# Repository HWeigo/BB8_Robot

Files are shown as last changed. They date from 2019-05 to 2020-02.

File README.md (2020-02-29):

# BB-8 Robot  
##### Keep Calm and May the Force Be With You  

## Overview  
This repository contains both codes and CAD model for the BB-8 robot. The main goal of this project is to redesign BB-8 robot’s inner mechanism, as well as the control algorithm, to improve its balance. A two-wheel self-balancing robot was built and tested first. After then, we reassemble it to the final BB-8 robot by changing the chassis and adding other components. STM32F407 was used as the microcontroller in this project, while CubeMX was utilized for STM32’s configuration and FreeRTOS was implemented as the kennel. /Model includes all the parts for both self-balancing car and our final BB-8 robot (based on SolidWorks 2018). Other electron components and stuffs are listed in /reference.  

## CAD and Physical Prototype

#### Two-wheel Self-balancing Robot
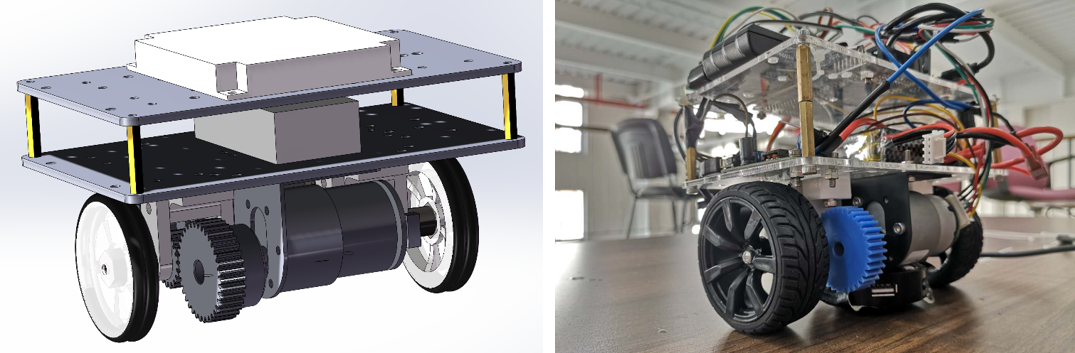
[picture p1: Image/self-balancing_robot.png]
Two-wheel Self-balancing Robot
  
#### BB-8 Robot
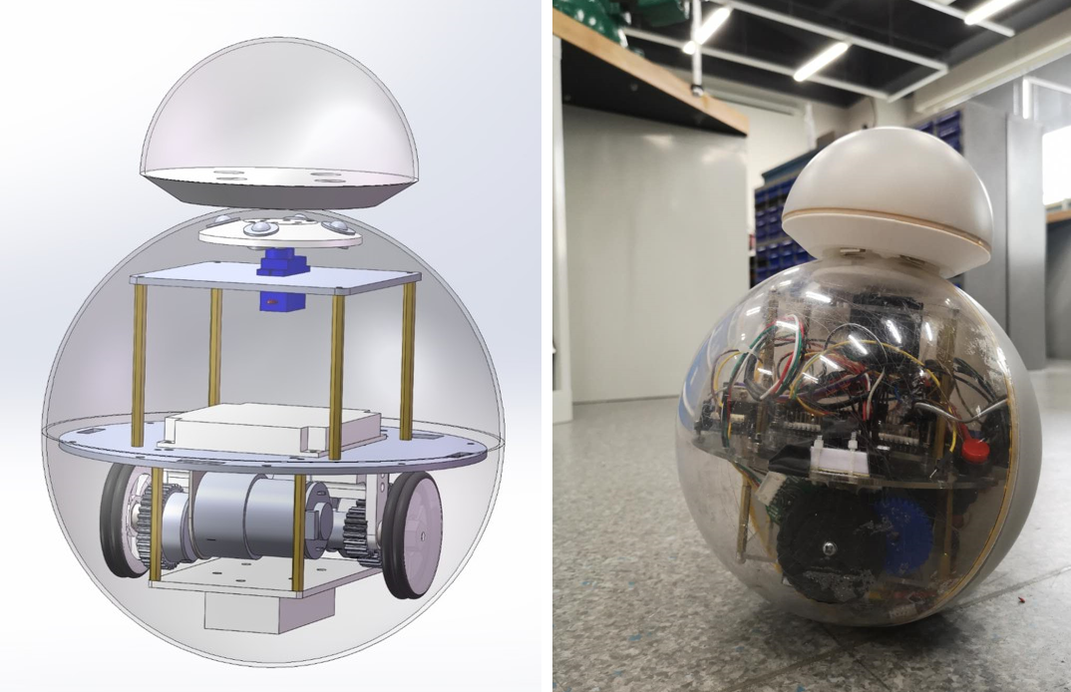
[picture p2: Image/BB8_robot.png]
BB-8 Robot
  

## Electronics Schematic  
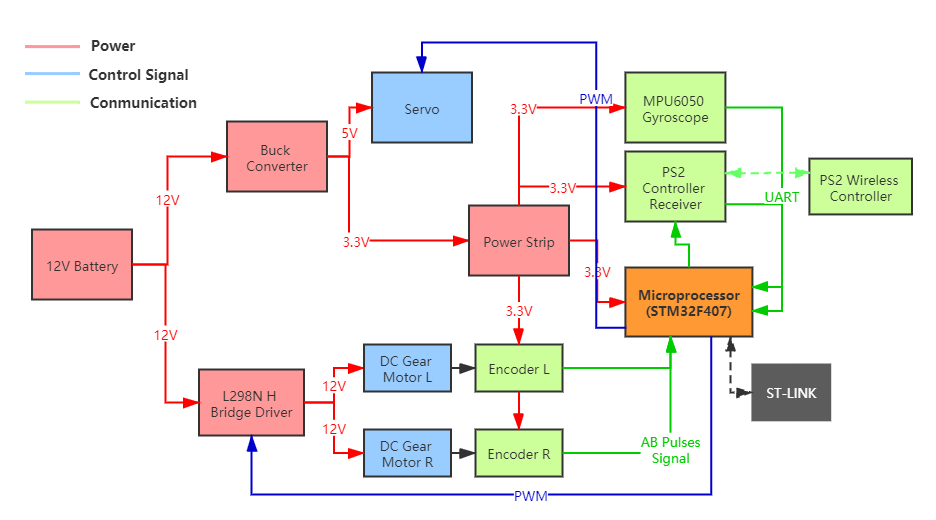
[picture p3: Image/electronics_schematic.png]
Electronics Schematic
  

## FreeRTOS Task Diagram  
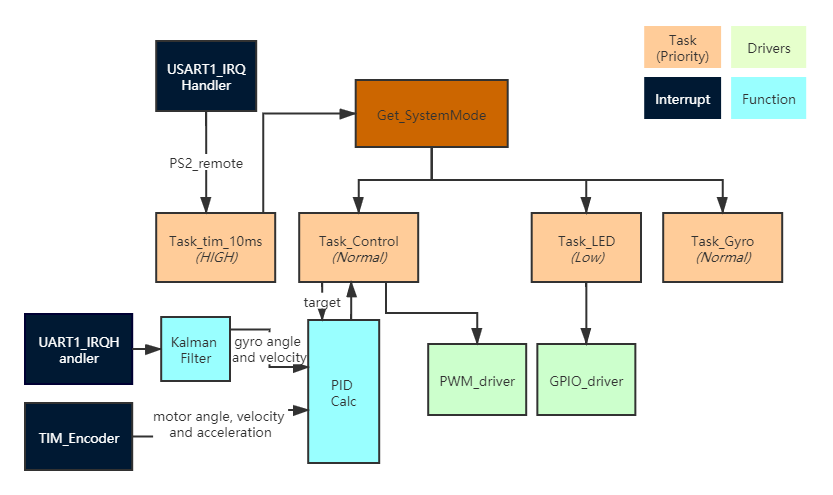
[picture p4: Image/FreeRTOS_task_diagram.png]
FreeRTOS Task Diagram


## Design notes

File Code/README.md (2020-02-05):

编译环境：Keil uVision5  
工程地址：./MDK-ARM/BB8_Robot.uvprojx  
底层文件：./Inc(声明文件)，./Src (主文件)  
任务文件：./Tasks/Inc (声明文件)，./Tasks/Src (主文件)  
  
STM32CubeMX配置文件：./BB8_Robot.ioc  
  
---
**操作方式**：  
PS2手柄：
左方向键：前后与旋转  
左摇杆：前后与旋转（无级变速）    
右摇杆：头部旋转（无级变速）  
右按键：自定义功能   
  
 ---
 
 **注意,每次使用STM32CubeMX配置后，需要：**  
```
  1,将/Application/User/freertos.c和/Application/User/main.c中的头文件声明删去，并改为#include "includes.h";
  2,将/Application/User/freertos.c中任务句柄删去（已转移到/Tasks下的任务当中）;
  3,检查是否有新引用内容，若有，添加到includes.h当中。
  ```

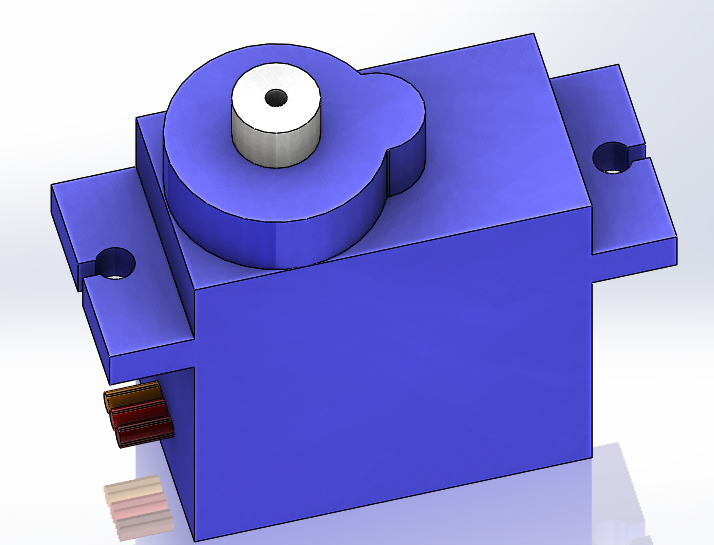
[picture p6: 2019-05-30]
Model/SG90.PNG

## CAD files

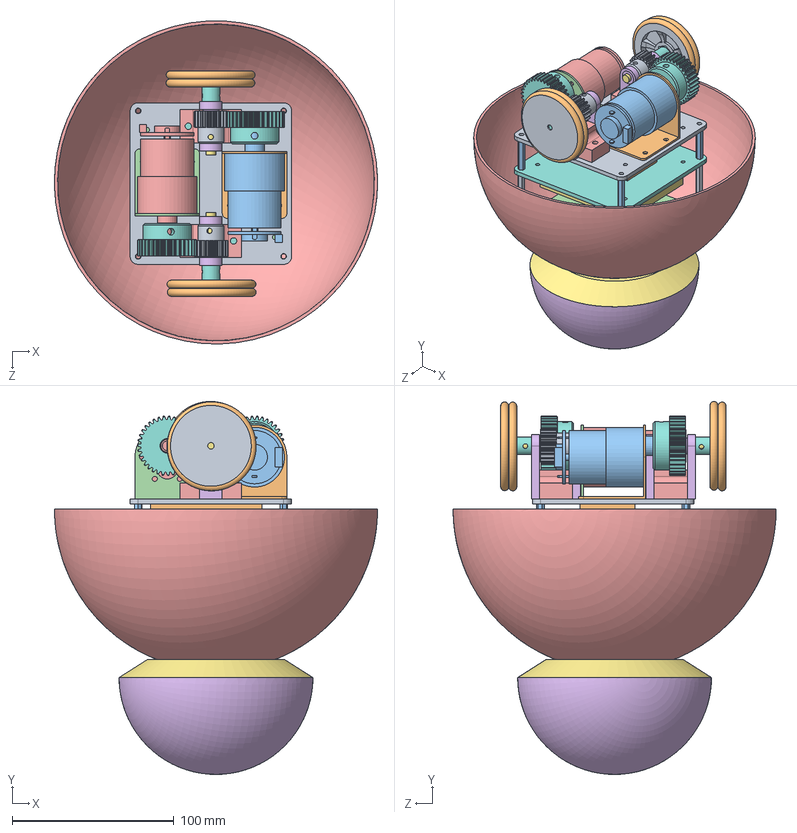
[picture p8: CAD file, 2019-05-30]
Model/初装.SLDASM
199.9 x 230.8 x 199.9 mm
平衡车电机座板
平衡车电机支架1
平衡车轮电机1
平衡车电机支架2
平衡车轮电机2
铜套 x 4
平衡车轮轴 x 2
联轴器1 x 2
轮子1 x 2
轮胎1 x 4
铜柱长 x 4
舵机座板
球壳小
头部底面
M1-35 x 2
M1-19(1) x 2
牛眼轮NL-8H x 8
舵机转板新
SG90
铜套座板连接板 x 2
铜套座板 x 4
主控板
主控座板
铜柱2 x 4
电池

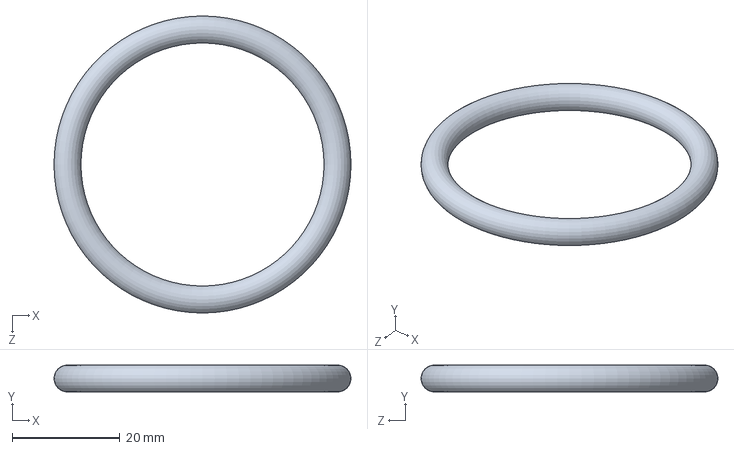
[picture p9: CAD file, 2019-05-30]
Model/轮胎2.SLDPRT
55.0 x 5.00 x 55.0 mm

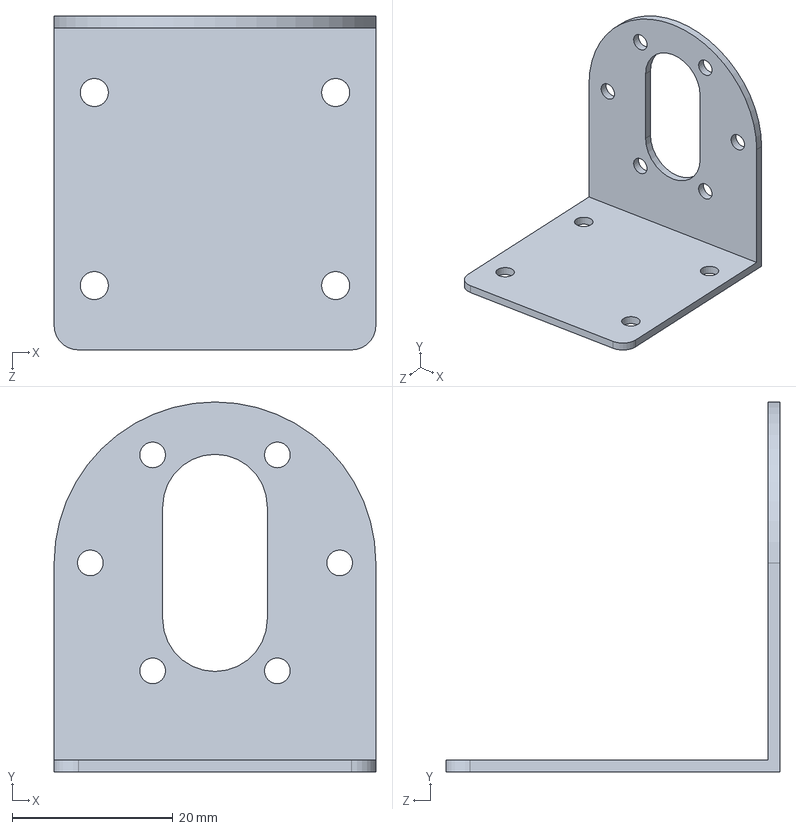
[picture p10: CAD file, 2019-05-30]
Model/平衡车电机支架1.SLDPRT
40.0 x 46.0 x 41.5 mm

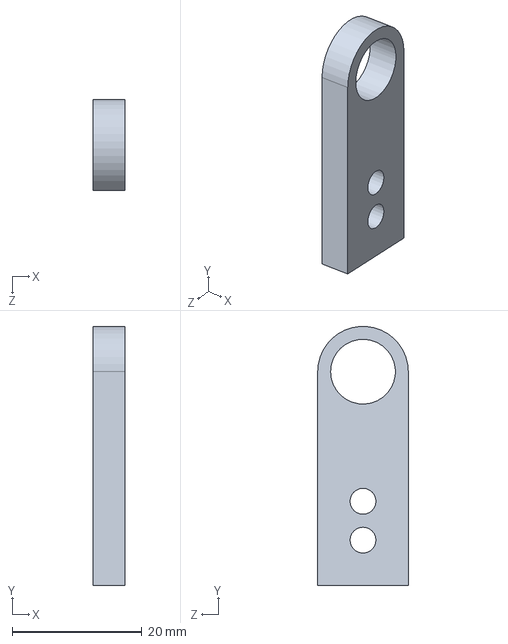
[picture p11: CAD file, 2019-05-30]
Model/铜套座板.SLDPRT
5.00 x 40.0 x 14.0 mm

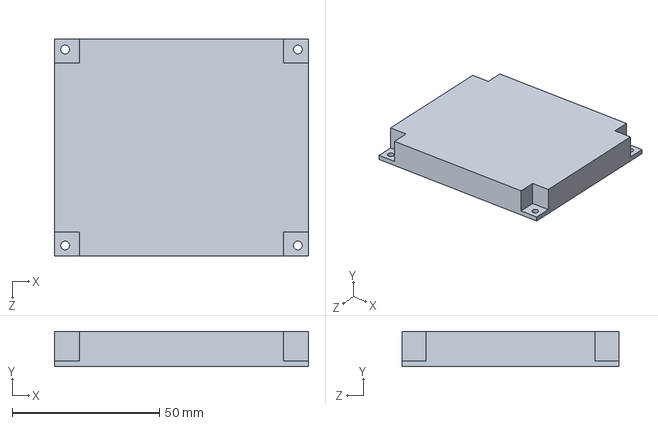
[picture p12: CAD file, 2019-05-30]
Model/主控板.SLDPRT
86.2 x 12.0 x 73.7 mm

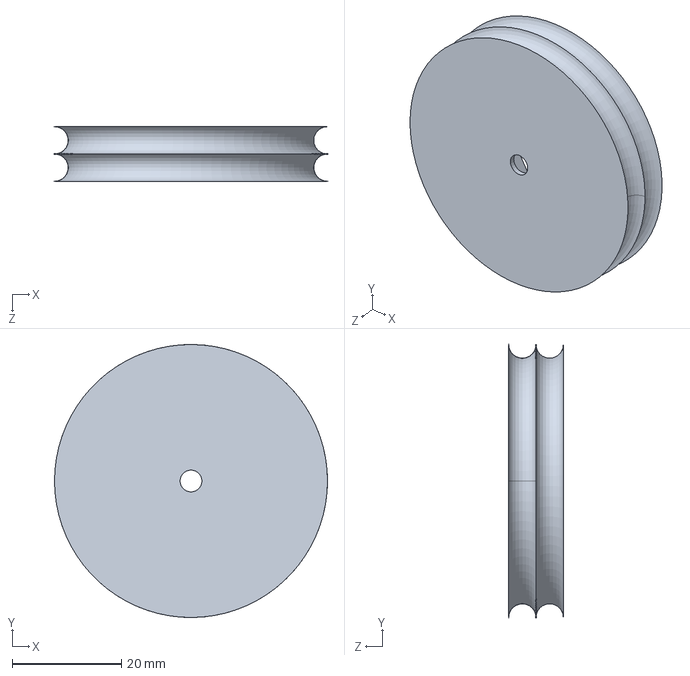
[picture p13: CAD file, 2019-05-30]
Model/轮子1.SLDPRT
50.0 x 50.0 x 10.0 mm

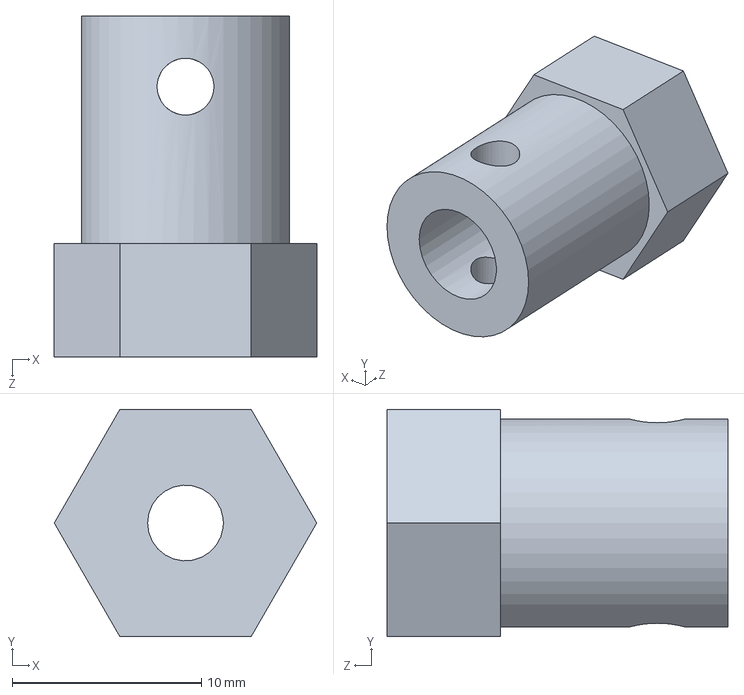
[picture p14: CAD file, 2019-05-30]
Model/联轴器2.SLDPRT
13.9 x 12.0 x 18.0 mm

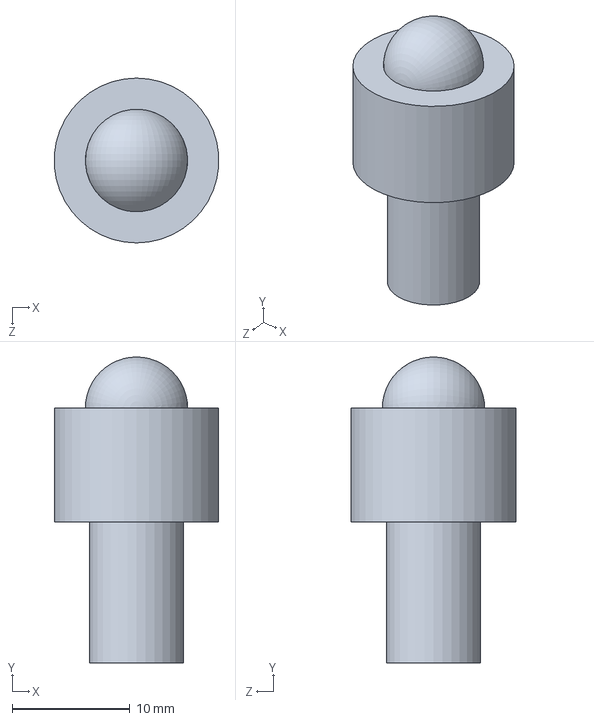
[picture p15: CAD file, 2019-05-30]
Model/小牛眼轮.SLDPRT
14.0 x 26.0 x 14.0 mm

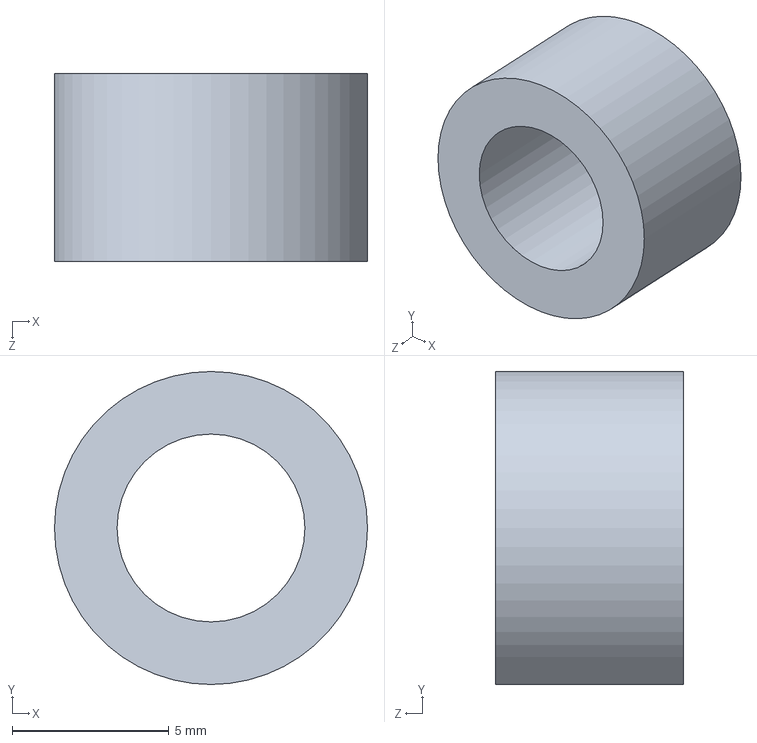
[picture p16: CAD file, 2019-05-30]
Model/铜套.SLDPRT
10.0 x 10.0 x 6.00 mm

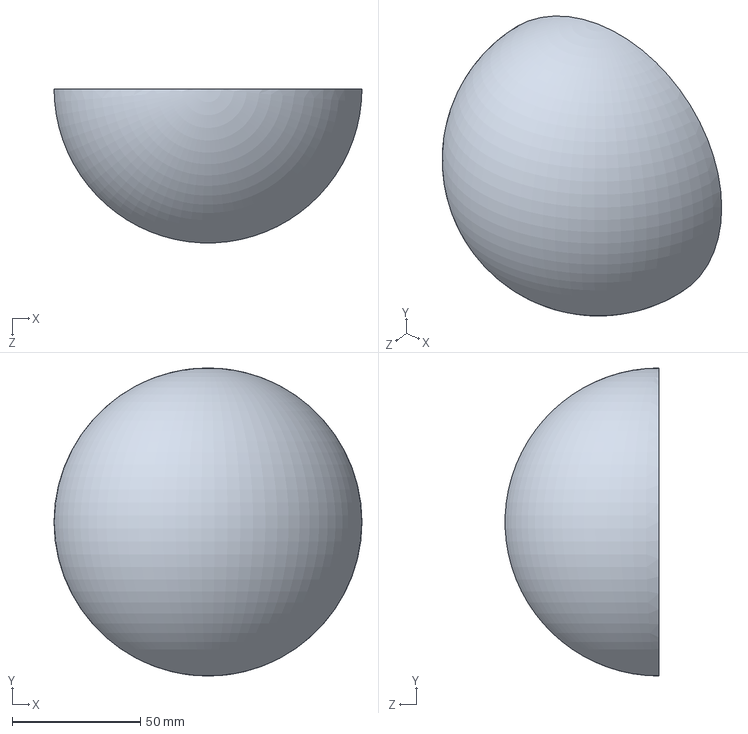
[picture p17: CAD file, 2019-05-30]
Model/球壳小.SLDPRT
120.0 x 120.0 x 59.9 mm

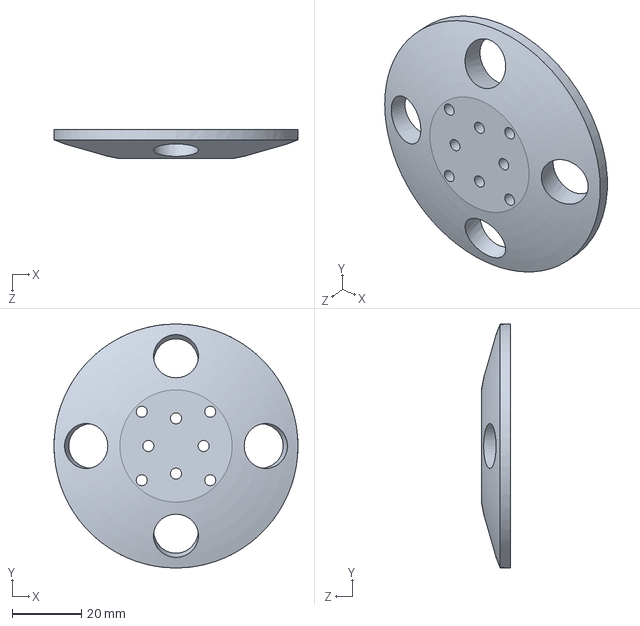
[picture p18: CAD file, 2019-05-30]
Model/舵机转板新.SLDPRT
70.6 x 70.6 x 8.50 mm

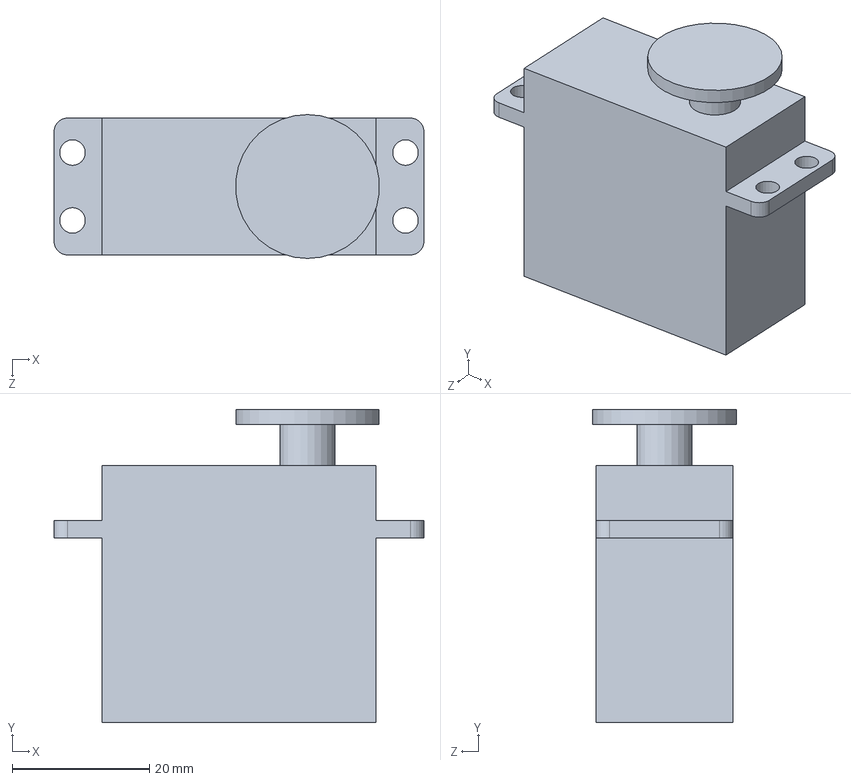
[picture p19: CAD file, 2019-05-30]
Model/舵机简图.SLDPRT
54.0 x 45.7 x 21.0 mm

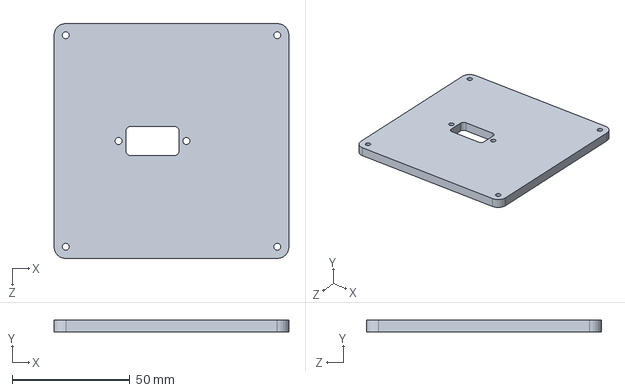
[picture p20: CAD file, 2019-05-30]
Model/舵机座板.SLDPRT
100.0 x 5.00 x 100.0 mm

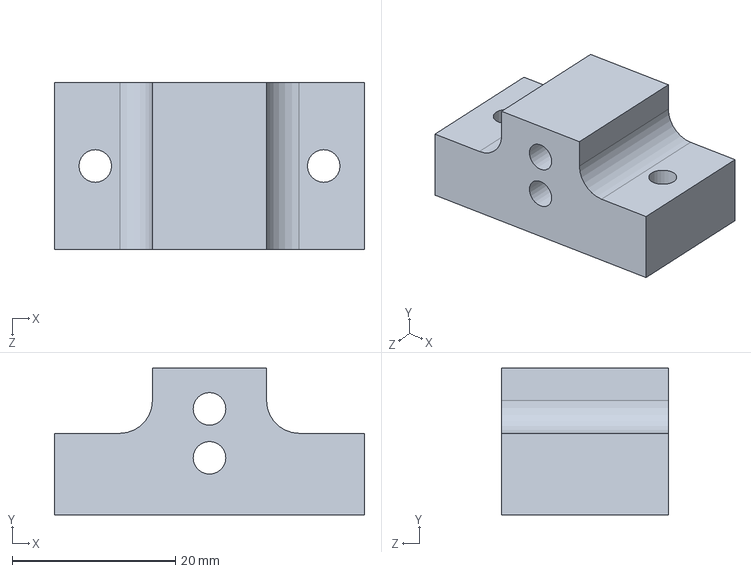
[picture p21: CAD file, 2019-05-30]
Model/铜套座板连接板.SLDPRT
38.0 x 18.0 x 20.5 mm

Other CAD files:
Model/联轴器1.SLDPRT
Model/轮胎1.SLDPRT
Model/SG90.SLDPRT
Model/铜柱长.SLDPRT
Model/M1-19(1).sldprt
Model/M1-35.SLDPRT
Model/一模凸台35.SLDPRT
Model/一模平齿轮15.SLDPRT
Model/主动旋转板.SLDPRT
Model/主控座板.SLDPRT
Model/原装轮子.SLDPRT
Model/头部底面.SLDPRT
Model/头部底面.STL
Model/头部底面旧.SLDPRT
Model/平衡车电机座板.SLDPRT
Model/平衡车电机支架2.SLDPRT
Model/平衡车轮电机1.SLDPRT
Model/平衡车轮电机2.SLDPRT
Model/平衡车轮轴.SLDPRT
Model/牛眼轮NL-8H.SLDPRT
Model/球壳1.SLDPRT
Model/电池.SLDPRT
Model/舵机转板新.STL
Model/轴承座.SLDPRT
Model/轴承座2.SLDPRT
Model/铜套座板连接板.STL
Model/铜柱2.SLDPRT

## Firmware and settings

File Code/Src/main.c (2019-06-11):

/**
  ******************************************************************************
  * @file           : main.c
  * @brief          : Main program body
  ******************************************************************************
  * This notice applies to any and all portions of this file
  * that are not between comment pairs USER CODE BEGIN and
  * USER CODE END. Other portions of this file, whether 
  * inserted by the user or by software development tools
  * are owned by their respective copyright owners.
  *
  * Copyright (c) 2019 STMicroelectronics International N.V. 
  * All rights reserved.
  *
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
  ******************************************************************************
  */
/* Includes ------------------------------------------------------------------*/
#include "includes.h"


/* USER CODE BEGIN PV */

/* USER CODE END PV */

void SystemClock_Config(void);
void MX_FREERTOS_Init(void);

/* USER CODE BEGIN PFP */

/* USER CODE END PFP */

/**
  * @brief  The application entry point.
  *
  * @retval None
  */
int main(void)
{
  /* MCU Configuration----------------------------------------------------------*/

  /* Reset of all peripherals, Initializes the Flash interface and the Systick. */
  HAL_Init();

  /* Configure the system clock */
  SystemClock_Config();

  /* Initialize all configured peripherals */
  MX_GPIO_Init();
  MX_DMA_Init();
  MX_USART1_UART_Init();
  MX_TIM2_Init();
  MX_TIM14_Init();
  MX_IWDG_Init();
  MX_TIM4_Init();
  MX_TIM5_Init();
  MX_TIM3_Init();
  /* USER CODE BEGIN 2 */

  HAL_TIM_PWM_Start(&htim2,TIM_CHANNEL_3);
	HAL_TIM_PWM_Start(&htim4,TIM_CHANNEL_1);
	HAL_TIM_PWM_Start(&htim4,TIM_CHANNEL_2);
	HAL_TIM_PWM_Start(&htim4,TIM_CHANNEL_3);
	HAL_TIM_PWM_Start(&htim4,TIM_CHANNEL_4);
	
	HAL_TIM_Encoder_Start(&htim3, TIM_CHANNEL_ALL);
	HAL_TIM_Encoder_Start(&htim5, TIM_CHANNEL_ALL);
  /* USER CODE END 2 */

  /* Call init function for freertos objects (in freertos.c) */
  MX_FREERTOS_Init();

  /* Start scheduler */
  osKernelStart();
  
  /* We should never get here as control is now taken by the scheduler */

  /* Infinite loop */
  /* USER CODE BEGIN WHILE */
	
  while (1)
  {

  /* USER CODE END WHILE */

  /* USER CODE BEGIN 3 */


  }
  /* USER CODE END 3 */

}

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
/**
  * @brief  Period elapsed callback in non blocking mode
  * @note   This function is called  when TIM1 interrupt took place, inside
  * HAL_TIM_IRQHandler(). It makes a direct call to HAL_IncTick() to increment
  * a global variable "uwTick" used as application time base.
  * @param  htim : TIM handle
  * @retval None
  */
void HAL_TIM_PeriodElapsedCallback(TIM_HandleTypeDef *htim)
{
  if (htim->Instance == TIM1) {
    HAL_IncTick();
  }
}

/**
  * @brief  This function is executed in case of error occurrence.
  * @param  file: The file name as string.
  * @param  line: The line in file as a number.
  * @retval None
  */
void _Error_Handler(char *file, int line)
{
  /* USER CODE BEGIN Error_Handler_Debug */
  /* User can add his own implementation to report the HAL error return state */
  while(1)
  {
  }
  /* USER CODE END Error_Handler_Debug */
}

#ifdef  USE_FULL_ASSERT
/**
  * @brief  Reports the name of the source file and the source line number
  *         where the assert_param error has occurred.
  * @param  file: pointer to the source file name
  * @param  line: assert_param error line source number
  * @retval None
  */
void assert_failed(uint8_t* file, uint32_t line)
{ 
  /* USER CODE BEGIN 6 */
  /* User can add his own implementation to report the file name and line number,
     tex: printf("Wrong parameters value: file %s on line %d\r\n", file, line) */
  /* USER CODE END 6 */
}
#endif /* USE_FULL_ASSERT */

/**
  * @}
  */

/**
  * @}
  */

/************************ (C) COPYRIGHT STMicroelectronics *****END OF FILE****/

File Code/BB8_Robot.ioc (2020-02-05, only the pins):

Mcu.UserName=STM32F407ZGTx
PA0-WKUP.Signal=S_TIM5_CH1
PA1.Signal=S_TIM5_CH2
PA10.Signal=USART1_RX
PA2.Signal=S_TIM2_CH3
PA3.Signal=S_TIM2_CH4
PA6.Signal=S_TIM3_CH1
PA7.Signal=S_TIM3_CH2
PA9.Signal=USART1_TX
PB12.GPIO_Label=DI
PB12.Signal=GPIO_Input
PB13.GPIO_Label=DO
PB13.Signal=GPIO_Output
PB14.GPIO_Label=CS
PB14.Signal=GPIO_Output
PB15.GPIO_Label=CLK
PB15.Signal=GPIO_Output
PD12.Signal=S_TIM4_CH1
PD13.Signal=S_TIM4_CH2
PD14.Signal=S_TIM4_CH3
PD15.Signal=S_TIM4_CH4
PE14.GPIO_Label=HCSensor
PE14.Signal=GPIO_Input
PF10.GPIO_Label=LED2
PF10.Signal=GPIO_Output
PF9.GPIO_Label=LED1
PF9.Signal=GPIO_Output
PH0-OSC_IN.Signal=RCC_OSC_IN
PH1-OSC_OUT.Signal=RCC_OSC_OUT

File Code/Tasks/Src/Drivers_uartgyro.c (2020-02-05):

/**
  ******************************************************************************
  * File Name          : Drivers_uartgyro.c
  * Description        : 陀螺仪信号读取与解算
  ******************************************************************************
*/

#include "includes.h"

uint8_t tmp_gyro;

void InitGyroUart(void)
{
	if(HAL_UART_Receive_DMA(&GYRO_UART,&tmp_gyro,1) != HAL_OK)
	{
		Error_Handler();
	}
}

uint8_t gyro_receiving = 0;
uint8_t gyroBuffer[80] = {0};
uint8_t gyroBuffercnt = 0;
uint8_t gyroID = 0;
uint8_t gyroIsReady = 0;
float gyroXAngle,gyroYAngle,gyroZAngle;
float gyroXspeed,gyroYspeed,gyroZspeed;
float gyroXacceleration,gyroYacceleration,gyroZacceleration;
float temperature;

void gyroUartRxCpltCallback(void)
{
//	if(HAL_UART_Receive_DMA(&GYRO_UART, &tmp_gyro, 1) != HAL_OK)
//	{
//		Error_Handler();
//	}
	if(gyro_receiving)
	{
		gyroBuffer[gyroBuffercnt] = tmp_gyro;
		gyroBuffercnt++;
		if(gyroBuffercnt > 20)
		{
			gyro_receiving = 0;
//			gyroBuffercnt = 0;
		}
		if(gyroBuffercnt == 11)
		{
//			gyroIsReady = 1;
//			gyro_receiving = 0;
//			gyroBuffercnt = 0;
			if(!sumCheck())
			{
				if(gyroBuffer[1] == 0x53)
				{
					gyroXAngle = (0x00|(gyroBuffer[3]<<8)|(gyroBuffer[2]))/32768.0f*180.0f;
					gyroYAngle = ((short)(0x00|(gyroBuffer[5]<<8)|(gyroBuffer[4])))/32768.0f*180.0f;
					gyroZAngle = (0x00|(gyroBuffer[7]<<8)|(gyroBuffer[6]))/32768.0f*180.0f;
				}
				else if(gyroBuffer[1] == 0x52)
				{
					gyroXspeed = ((short)(gyroBuffer[3]<<8)|gyroBuffer[2])/32768.0f*2000.0f;
					gyroYspeed = ((short)(gyroBuffer[5]<<8)|gyroBuffer[4])/32768.0f*2000.0f;
					gyroZspeed = ((short)(gyroBuffer[7]<<8)|gyroBuffer[6])/32768.0f*2000.0f;
				}
			}
			gyro_receiving = 0;
		}
	}
	else 
	{
		if(tmp_gyro == 0x55)
		{
			gyro_receiving = 1;
			gyroBuffercnt = 0;
			gyroBuffer[gyroBuffercnt] = tmp_gyro;
			++gyroBuffercnt;
		}
	}
		if(HAL_UART_Receive_DMA(&GYRO_UART, &tmp_gyro, 1) != HAL_OK)
		{
			Error_Handler();
	  }
//	if(gyroIsReady && !sumCheck())
//	{
////			printf("Processing gyro.");      //开苃后dubug有问题，未解决
//		switch(gyroBuffer[1])
//		{
//			case 0x51:
//			{
//				gyroXacceleration = ((short)(gyroBuffer[3]<<8)|gyroBuffer[2])/32768.0f*16.0f;
//				gyroYacceleration = ((short)(gyroBuffer[5]<<8)|gyroBuffer[4])/32768.0f*16.0f;
//				gyroZacceleration = ((short)(gyroBuffer[7]<<8)|gyroBuffer[6])/32768.0f*16.0f;
//				
//				temperature = ((short)(gyroBuffer[9]<<8|gyroBuffer[8]))/340.0f + 36.25f;
//			}break;
//			case 0x52:
//			{
//				gyroXspeed = ((short)(gyroBuffer[3]<<8)|gyroBuffer[2])/32768.0f*2000.0f;
//				gyroYspeed = ((short)(gyroBuffer[5]<<8)|gyroBuffer[4])/32768.0f*2000.0f;
//				gyroZspeed = ((short)(gyroBuffer[7]<<8)|gyroBuffer[6])/32768.0f*2000.0f;
//			}break;
//			case 0x53:
//			{
//				gyroXAngle = ((short)(0x00|gyroBuffer[3]<<8|gyroBuffer[2]))/32768.0f*180.0f;
//				gyroYAngle = ((short)(0x00|gyroBuffer[5]<<8|gyroBuffer[4]))/32768.0f*180.0f;
//				gyroZAngle = ((short)(0x00|gyroBuffer[7]<<8|gyroBuffer[6]))/32768.0f*180.0f;
//			}break;
//			default:
//				Error_Handler();
//		}
//	}
//					
//	gyroIsReady = 0;
}


void HAL_UART_RxCpltCallback(UART_HandleTypeDef *UartHandle)
{
	if(UartHandle == &GYRO_UART)
	{
		gyroUartRxCpltCallback();
	}
}   

uint8_t minus;
uint8_t sumCheck(void)
{
		minus = gyroBuffer[10];
		for(int i=0;i<10;i++)
		{
			minus -= gyroBuffer[i];
		}
		return minus;
}

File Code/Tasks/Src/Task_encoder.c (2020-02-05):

/**
  ******************************************************************************
  * File Name          : Task_LED.c
  * Description        : LED灯闪烁，对应板子上PF9,PF10
	* 位于最低优先级＃用于监测系统时间调度情况以及是否宕机。
  ******************************************************************************
  */
#include "includes.h"

//int32_t encoderL= 0, encoderR = 0;

//void Task_encoder(void const * argument)
//{
//  /* USER CODE BEGIN Task_encoder */
//  /* Infinite loop */
//	portTickType xLastWakeTime;
//	xLastWakeTime = xTaskGetTickCount();
//	
//  while(1)
//  {
//		if(__HAL_TIM_DIRECTION_STATUS(&htim5)==0)	encoderL=__HAL_TIM_GetCounter(&htim5);
//		else if(__HAL_TIM_GetCounter(&htim5)!=0)	encoderL=-(0xFFFF-__HAL_TIM_GetCounter(&htim5)+1);
//		if(__HAL_TIM_DIRECTION_STATUS(&htim3)==0)	encoderR=__HAL_TIM_GetCounter(&htim3);
//		else if(__HAL_TIM_GetCounter(&htim3)!=0)	encoderR=-(0xFFFF-__HAL_TIM_GetCounter(&htim3)+1);		
//		
//		
//		__HAL_TIM_SetCounter(&htim5,0);
//		__HAL_TIM_SetCounter(&htim3,0);
//		
//		vTaskDelayUntil( &xLastWakeTime, ( 45 / portTICK_RATE_MS ) ); //进入阻塞态50ms
//    //osDelay(10);
//  }
//  /* USER CODE END Task_encoder */
//}

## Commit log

2019-05-01 框架搭建
2019-05-01 Cube配置UART1DMA中断开启
2019-05-01 IMU调通
2019-05-01 增添区块Model
2019-05-01 Model添加文件
2019-05-01 初始化闪灯
2019-05-02 优化gyro uart中断读取
    每次cube配置完注意要把freertos.c main.c中的头文件声明改为includes.h
2019-05-02 将gyro数据处理与中断读取分离
    数据在中断中读取，在Task_gyro中处理
2019-05-09 360°舵机调通 Task_servo
2019-05-09 SYSCLK PLL倍频至96MHz
    时钟源HSI
2019-05-12 ps2驱动未完成
2019-05-18 Revert "ps2驱动未完成"
    This reverts commit 6c7161fc41532a9292cf8657d4b689a9fe696691.
    [BB8_Robot.ioc, Task_ps2.c, main.c]
2019-05-19 ps2手柄接收（一段时间后出现宕机）
    暂时没有与其他功能联合调试，仅仅测试了ps2手柄数据的读取。
    宕机原因暂时没有查明，似乎与任务分配的内存空间有关。
2019-05-20 添加看门狗
    暂时放在Task_LED中喂狗，建议之后改到定时中断当中。
    IWAG分频32，递减基础器重载值3000，即3000ms定时看门
2019-05-20 ps2接受异常问题解决&任务优先级更改
    手柄接受信号时需要关闭所有中断源！！
2019-05-21 头部舵机控制初步完成
    右摇杆x控制云台头部左右转动，三角形转头动作
2019-05-25 修改CubeMX中配置
    -调整任务优先级（ps2为最高优先级）
    -扩大任务堆栈空间
    -补充注释
2019-05-25 HC-SR501人体红外检测模块测试
    效果一般，存在延迟，调参不易，灵敏度难以估计
2019-05-25 配置TIM4作为底盘电机PWM驱动
    暂时放在Task_servo.c中测试，之后添加单独任务控制底盘电机。
2019-05-29 Model V1.0 by fyy
    基本建模完成
    [M1-19(1).sldprt, M1-35.SLDPRT, SG90.SLDPRT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]
2019-05-30 底盘电机PWM控制 ch1ch2测试完成
2019-05-30 TIM4ch3ch4配置测试完成
    暂时所有底盘电机控制都放在task_servo当中
2019-05-30 舵机PWM输出控制转移至TIM2ch3(PA2)
2019-05-31 TIM3,TIM5配置作Encoder模式
    未完成Encoder数据读取
2019-05-31 encoder读取程序编写，尚未测试
    新建文件encoder，编码器读取暂时放在task_gyro.c，osDelay(10)暂时改为osDelay(100)
2019-05-31 利用vTaskDelayUntil做编码器定时，未测试
2019-05-31 编码器读数程序转至Task_encoder，TIM5编码器读数测试完成
    Task_encoder刷新频率暂时为10ms
2019-06-05 TIM3编码器调通
2019-06-05 编码器每次读取后刷新
2019-06-10 Cube配置Encoder前 ps2手柄正常
2019-06-10 尚未配置Encoder任务
2019-06-11 PS2掉线问题解决
2019-06-12 添加直立环 手柄掉线/宕机与任务delay时间有关
2019-06-12 任务时间调整
    task_ps2间隔时间不能过长否则ps2长时间接受不到信号掉线
    task_gyro跟task_servo的osdelay时间若过短系统容易宕机
2019-06-12 反应灵敏，宕机频繁
2019-06-14 框架整体修改，合并高优先级，陀螺仪数据解算放至中断 by fyy
2019-06-21 PID调试
2019-06-24 平衡车终版
